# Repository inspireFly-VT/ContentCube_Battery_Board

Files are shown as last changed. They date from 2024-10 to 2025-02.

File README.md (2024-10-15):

View this project on [CADLAB.io](https://cadlab.io/project/28565). 

# battery_board
The battery and power management board for the PROVES Kit.
# Flight Heritage
| Version | Flights | Status |
| --- | --- | --- |
| V0 | Unflown | Not Supported |
| V1 | Unflown | Not Supported |
| V2 | Pleiades - Yearling, Pleaides - Squared | Supported |
| V3 | Planned Pleiades - Orpheus | In Development |
# Features
## battery_board_v2
The battery board flown on the Pleiades-Yearling and Pleiades-Squared missions. The board serves as an interface with the rest of the satellite. A 12 position picolock is utilized to interface between the Flight Controller and the Battery Board. The board interfaces with 5 solar faces of the satellite using 5 position picolocks. The other 2 position picolocks are used for interfacing with the inhibit scheme, battery heater, burn wire, and direct charging port. The hardware utilized on the module is the following:
- **LT3652 MPPT Solar Charger** is utilized to charge the batteries up from the solar faces. The Solar Charging circuitry should only allow higher potentials to be fed to the battery, and allow no reverse current into the charging circuitry.
- **PCA9685 LED Driver** is utilized to toggle the power to each of the solar faces. In the event that a sensor or other component fails on a face, it makes it possible to isolate the problem and power down the face.
- **TCA9548 I2C Multiplexer** is implemented to allow the use of a single I2C bus from the flight computer. This I2C bus can then get multiplexed to the solar faces. This allows the sensors on all of the faces to be the exact same, maintain the same addresses, and still be individually addressable. Two of the multiplexed lines are unused, 5 are used for each solar face, and 1 is used to breakout a stemma QT connection for additional sensors or I2C devices.
- **TPS54226PWP Switching Voltage Regulator** is utilized to maximize the efficiency of the system, and generate less heat central to the system. A 3.3V bus is created from the battery voltage and circuitry inspired by the PyCubed has been implemented to allow the satellite to reset the 3.3V bus. This functionality is known as the "One Shot" Regulator Reset that with a logic "High" applied, the 3.3V bus will shutdown and restart momentarily.
- **TPS7A4501 LDO Voltage Regulator** is implemented to supply 5V to the radio on the flight controller. This bus voltage can be toggled by an input taken from the flight controller.
- **(2) INA219 Power Monitors** are implemented to measure the power supplied from the solar cells, and the power dropped across the system. This data is fed back via the I2C bus to the flight controller
- **PTC2075 Temperature Sensor** is utilized to obtain ambient temperature readings from inside the satellite.
- **R5460N208AA** is utilized to disconnect the negative side of the batteries from the system in overcharge and overdischarge events.
- **APAN3109 Relay** is implemented to allow current to flow to the battery heater and burn wire MOSFETS.

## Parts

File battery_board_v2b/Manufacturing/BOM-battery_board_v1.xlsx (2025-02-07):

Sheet: battery_board_v2b
Id | Designator | Footprint | Quantity | Designation | JLC PN | Digikey PN | Inventory
3 | C1,C2 | C_0603_1608Metric | 2 | 22uF | C59461
31 | C10 | C_0603_1608Metric | 1 | 3.3nF | C1613
4 | C16,C15,C18,C12,C13 | C_0603_1608Metric | 5 | 10uF | C19702
8 | C17,C11 | C_0603_1608Metric | 2 | 1uF | C15849
60 | C22,C27 | C_0402_1005Metric_Pad0.74x0.62mm_HandSolder | 2 | 0.1uF | C60474
64 | C23,C21 | C_0402_1005Metric_Pad0.74x0.62mm_HandSolder | 2 | 0.01uF | C272878
48 | C24 | C_0402_1005Metric_Pad0.74x0.62mm_HandSolder | 1 | 1uF | C77006
35 | C26,C25 | C_0402_1005Metric_Pad0.74x0.62mm_HandSolder | 2 | 10uF | C15525
33 | C3,C4 | C_1210_3225Metric | 2 | 100uF | C23742
25 | C5,C6,C8,C9,C20,C7,C14 | C_0603_1608Metric | 7 | 0.1uF | C14663
71 | D3,D1 | DIOM5226X262N | 2 | D_Schottky | C2892544
6 | D5,D2,D4 | PWRDI-123 | 3 | DFLS130L | C110493
12 | FB1,FB3,FB2 | R_0603_1608Metric | 3 | FerriteBead |  | 490-5258-1-ND | 15 | “+3”
73 | IC1 | SOP65P640X110-28N | 1 | PCA9685PW,118 | C2678753
65 | IC2 | SOP65P490X110-13N | 1 | LT3652IMSE#PBF |  | 505-LT3652IMSE#PBF-ND
70 | IC3 | TSSOP-8_3x3mm_P0.65mm | 1 | PCT2075DP,118 | C192518
56 | J1 | MOLEX_5040500591 | 1 | Face0 |  | WM24877CT-ND
13 | J11,J13,J14,J15,J16,J17 | MOLEX_504050-0291 | 1 | CHARGE |  | WM25693CT-ND | 50
41 | J18 | PinSocket_1x02_P2.54mm_Vertical | 1 | Bypass
18 | J19 | MOLEX_504050-0291 | 1 | Heater |  | WM25693CT-ND
62 | J2,J3,J4 | MOLEX_5040500591 | 1 | Face1 |  | WM24877CT-ND | 25
5 | J6 | Molex_Pico-Lock_504050-1291_1x12-1MP_P1.50mm_Horizontal | 1 | FC_FACE |  | WM16219CT-ND | 5
26 | J7 | MOLEX_504050-0291 | 1 | 5V Breakout |  | WM25693CT-ND
54 | J8 | MOLEX_504050-0291 | 1 | ISS |  | WM25693CT-ND
57 | J9 | MOLEX_504050-0291 | 1 | TC |  | WM25693CT-ND
67 | K1 | RELAY_APAN3105 | 1 | APAN3105 |  | 255-5324-5-ND | 5
58 | L1 | L_1812_4532Metric | 1 | 3.3uH |  | 732-3063-1-ND | 5
59 | L2 | L_1812_4532Metric | 1 | 10uH |  | 732-3067-1-ND | 5
9 | Q2,Q1 | SOIC-8_3.9x4.9mm_P1.27mm | 2 | IRF7458 | C10879
11 | Q3,Q4 | SOT-363_SC-70-6 | 2 | MBT2222ADW1T1 | C157366
30 | Q6,Q9 | NDS8434 | 2 | SQ4401CEY-T1_GE3 |  | 742-SQ4401CEY-T1_GE3CT-ND | 4
10 | Q7 | SOT-523 | 1 | MMBT2222AT |  | MMBT2222ALT1GOSCT-ND | 5
49 | Q8,Q5 | SOT-23 | 2 | IRLML2803 | C2590
52 | R1 | R_2512_6332Metric | 1 | 0.01 |  | P19181CT-ND | 5
50 | R10 | R_0603_1608Metric | 1 | 20K | C408766
2 | R14,R40,R39,R50 | R_0603_1608Metric | 4 | 10k | C25804
20 | R2 | R_0603_1608Metric | 1 | 1K | C21190
53 | R22,R37 | R_2512_6332Metric | 2 | 0.002 |  | P17090CT-ND | 10
16 | R31 | R_0603_1608Metric | 1 | 3.3K | C22978
36 | R32 | R_0603_1608Metric | 1 | 200k | C25811
28 | R33 | R_0603_1608Metric | 1 | 85k |  | 2019-RN73R1JTTD8562F100CT-ND | 5
19 | R34,R44 | R_0603_1608Metric | 2 | 634k | C321970
74 | R35 | R_0603_1608Metric | 1 | 412k | C403212
63 | R36 | R_2512_6332Metric | 1 | 0.1 |  | YAG2159CT-ND | 10
46 | R4,R3 | R_0603_1608Metric | 2 | 330 | C23138
7 | R41,R16 | R_0603_1608Metric | 2 | 4.7k | C23162
66 | R42,R17,R9,R8,R11,R12,R13 | R_0603_1608Metric | 7 | 100k | C81751
1 | R43,R28,R25,R29,R19,R21,R30,R26,R15,R20,R23,R18,R27,R38,R24 | R_0603_1608Metric | 15 | 10K | C95204
24 | R46 | R_0402_1005Metric_Pad0.72x0.64mm_HandSolder | 1 | 1-MOhm | C93949
14 | R47,R48 | R_0402_1005Metric_Pad0.72x0.64mm_HandSolder | 2 | 100-Ohm | C106232
47 | R49 | R_0402_1005Metric_Pad0.72x0.64mm_HandSolder | 1 | 1k | C136974
45 | R6,R5 | R_0603_1608Metric | 2 | 73.2K | C861548
39 | R7 | R_0603_1608Metric | 1 | 22.1K | C137768
44 | U1 | R5460N233AF-SOT95P280X130-6N | 1 | R5460N208AA | C259714
29 | U10 | SOT-23 | 1 | TLVH431 DBZ SOT-23 |  | 296-36778-1-ND | 5
69 | U11 | TSSOP-10_3x3mm_P0.5mm | 1 | ADS1015IDGS |  | 296-25227-1-ND | 5
40 | U2 | PWP14_2P31X2P46-L | 1 | TPS54226PWPRPWP14_2P31X2P46-L |  | 296-25332-1-ND | 5
42 | U4 | SOP65P640X120-24N | 1 | TCA9548APWR | C130026
38 | IC4 | TPSM84209RKHT | 1 | TPSM84209RKHT | C2836944
55 | U6,U3 | SOIC-8_3.9x4.9mm_P1.27mm | 2 | INA219AxD | C138706
75 | U8,U7 | 1049 | 2 | 1049 |  | 36-1049-ND | 10
22 | U9 | MSOP-8_3x3mm_P0.65mm | 1 | AD8495 |  | AD8495ARMZ-R7CT-ND | 5
 | C19 | C_0603_1608Metric | 1 | 330pF | C1664
 | C28 | C_0603_1608Metric | 1 | 47uF | C140782
 | R45 | R_0603_1608Metric | 1 | 1.37k | C137777
 | Tool Hand Extractor |  |  |  |  |  | 1
 | Connection Socket 30 – 32AWG |  |  |  |  |  | 250
 | CONN RCPT HSG 2POS 1.50MM |  |  |  |  |  | 50
 | CONN RCPT HSG 4POS 1.50MM |  |  |  |  |  | 10
 | CONN RCPT HSG 5POS 1.50MM |  |  |  |  |  | 25
 | CONN RCPT HSG 6POS 1.50MM |  |  |  |  |  | 10
 | CONN RCPT HSG 12POS 1.50MM |  |  |  |  |  | 10

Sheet: BOM-battery_board_v1
Designation | Designator | Footprint | Supplier and ref
73.2K | R6,R5 | R_0603_1608Metric | C101180
100-Ohm | R47,R48 | R_0402_1005Metric_Pad0.72x0.64mm_HandSolder | C106232
IRF7458 | Q2,Q1 | SOIC-8_3.9x4.9mm_P1.27mm | C10879
22uF | C1,C2 | C_0603_1608Metric | C109448
DFLS130L | D5,D2,D4 | PWRDI-123 | C110493
TCA9548APWR | U4 | SOP65P640X120-24N | C130026
ADS1015IDGS | U11 | TSSOP-10_3x3mm_P0.5mm | C1355858
1k | R49 | R_0402_1005Metric_Pad0.72x0.64mm_HandSolder | C136974
INA219AxD | U6,U3 | SOIC-8_3.9x4.9mm_P1.27mm | C138706
22.1K | R7 | R_0603_1608Metric | C137768
0.1uF | C5,C6,C8,C9,C20,C7,C14 | C_0603_1608Metric | C14663
MBT2222ADW1T1 | Q3,Q4 | SOT-363_SC-70-6 | C157366
1uF | C17,C11 | C_0603_1608Metric | C15849
3.3nF | C10 | C_0603_1608Metric | C1613
PCT2075DP,118 | IC3 | TSSOP-8_3x3mm_P0.65mm | C192518
10uF | C16,C15,C18,C12 | C_0603_1608Metric | C19702
1K | R2 | R_0603_1608Metric | C21190
3.3K | R31 | R_0603_1608Metric | C22978
330 | R4,R3 | R_0603_1608Metric | C23138
4.7k | R41,R16 | R_0603_1608Metric | C23162
200uF | C19,C13 | C_1210_3225Metric | C23742
100uF | C3,C4 | C_1210_3225Metric | C23742
10k | R14,R40,R39 | R_0603_1608Metric | C25804
200k | R32 | R_0603_1608Metric | C25811
IRLML2803 | Q8,Q5 | SOT-23 | C2590
R5460N208AA | U1 | R5460N233AF-SOT95P280X130-6N | C259714
PCA9685PW,118 | IC1 | SOP65P640X110-28N | C2678753
0.01uF | C23,C21 | C_0402_1005Metric_Pad0.74x0.62mm_HandSolder | C272878
D_Schottky | D3,D1 | DIOM5226X262N | C2892544
412k | R35 | R_0603_1608Metric | C403212
634k | R34,R44 | R_0603_1608Metric | C321970
20K | R10 | R_0603_1608Metric | C408766
0.1uF | C22,C27 | C_0402_1005Metric_Pad0.74x0.62mm_HandSolder | C60474
1uF | C24 | C_0402_1005Metric_Pad0.74x0.62mm_HandSolder | C77006
100k | R42,R17,R9,R8,R11,R12,R13 | R_0603_1608Metric | C81751
TPS7A4501DCQT | U5 | TPS7A4501DCQT | C840094
1-MOhm | R46 | R_0402_1005Metric_Pad0.72x0.64mm_HandSolder | C93949
10K | R43,R28,R25,R29,R19,R21,R30,R26,R15,R20,R23,R18,R27,R38,R24 | R_0603_1608Metric | C95204
10uF | C26,C25 | C_0402_1005Metric_Pad0.74x0.62mm_HandSolder | C962136

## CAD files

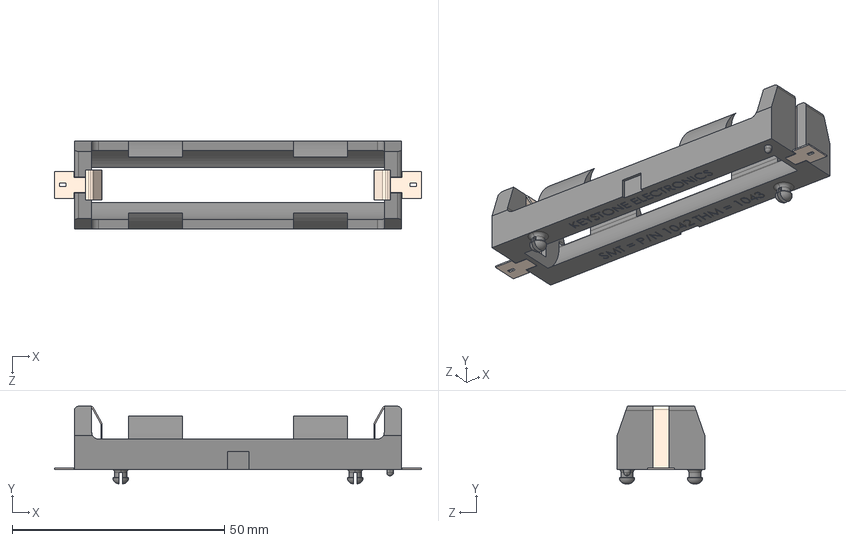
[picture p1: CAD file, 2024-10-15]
battery_board_v2b/Footprints/1042 (NOT OPEN SOURCE)/1042.stp
86.4 x 18.3 x 20.6 mm

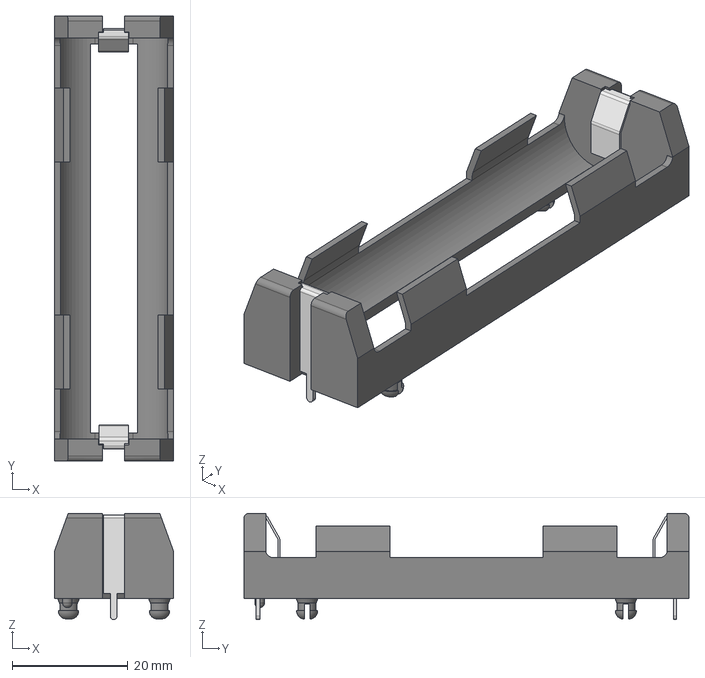
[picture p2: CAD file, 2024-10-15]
battery_board_v2b/Footprints/1043 (NOT OPEN SOURCE)/1043.stp
20.6 x 77.0 x 18.4 mm

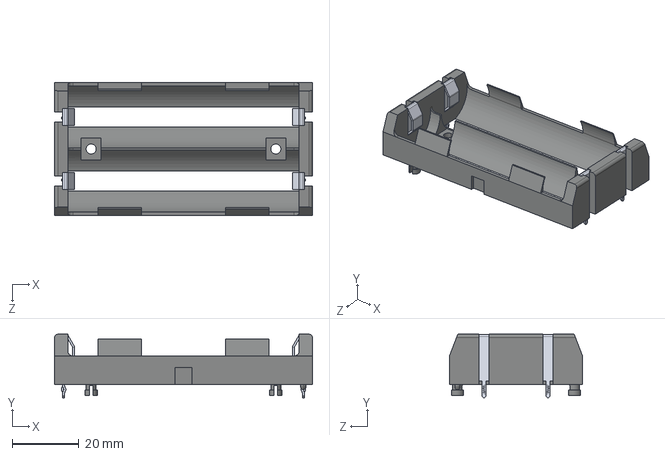
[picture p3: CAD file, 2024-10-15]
battery_board_v2b/Footprints/1049 (NOT OPEN SOURCE)/3D/1049.stp
77.1 x 19.0 x 39.8 mm

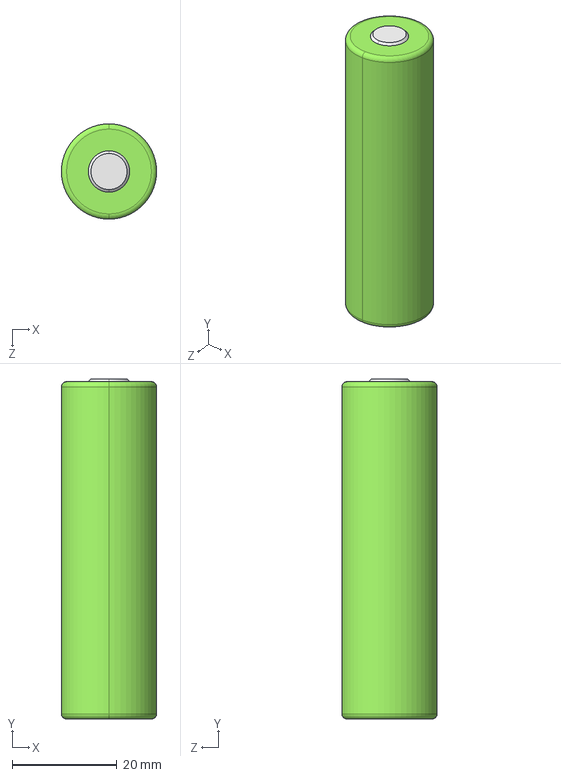
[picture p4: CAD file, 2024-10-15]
battery_board_v2b/Footprints/18650/Panasonic_NCR18650B_Battery-Gabriella.STEP
18.2 x 64.9 x 18.2 mm

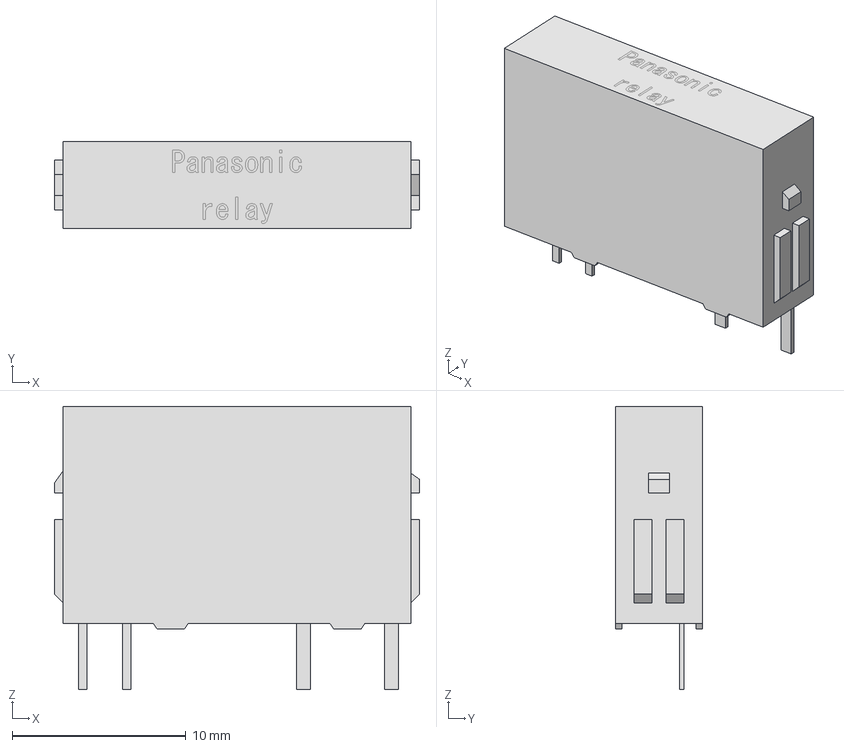
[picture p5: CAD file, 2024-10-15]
battery_board_v2b/Footprints/APAN/apan31・・.step
21.0 x 5.00 x 16.3 mm

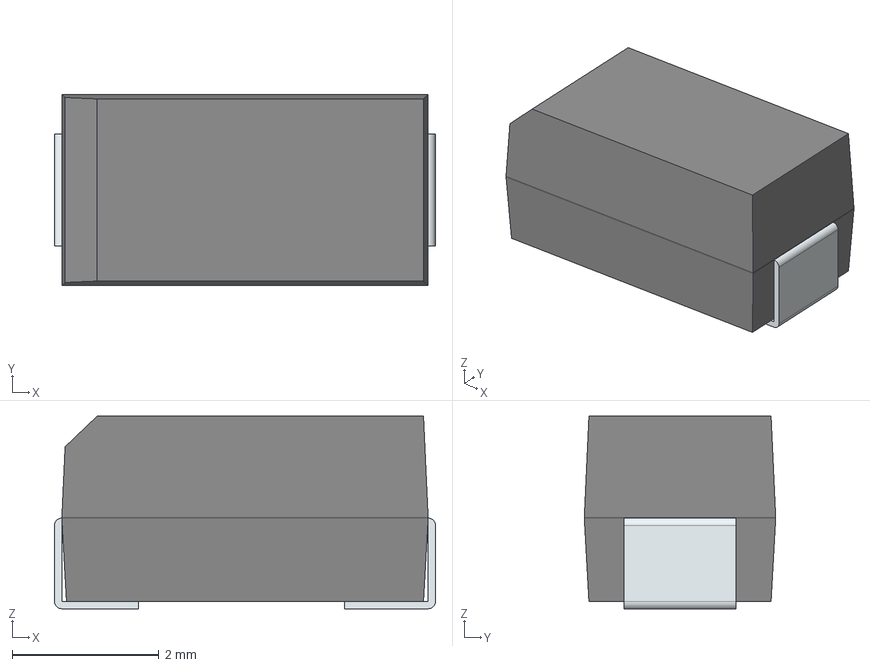
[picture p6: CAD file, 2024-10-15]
battery_board_v2b/Footprints/LIB_CMSH3-40MA_TR13_PBFREE/CMSH3-40MA_TR13_PBFREE/3D/CMSH3-40MA_TR13_PBFREE.stp
5.18 x 2.60 x 2.62 mm
FilletPin1
FilletPin2

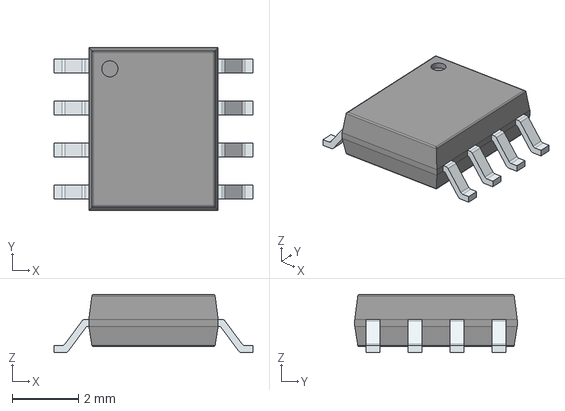
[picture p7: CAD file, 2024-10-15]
battery_board_v2b/Footprints/LIB_IRF7105TRPBF/IRF7105TRPBF/3D/IRF7105TRPBF.stp
6.00 x 4.90 x 1.75 mm
PinsArrayLR

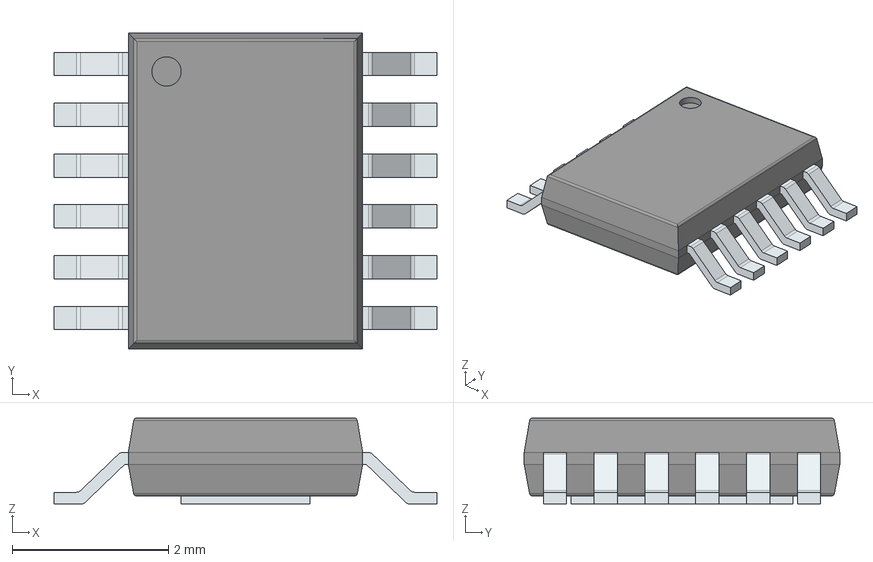
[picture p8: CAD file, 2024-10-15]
battery_board_v2b/Footprints/LIB_LT3652IMSE#PBF/LT3652IMSE#PBF/3D/LT3652IMSE#PBF.stp
4.90 x 4.04 x 1.10 mm
PinsArrayLR
ThermalPad

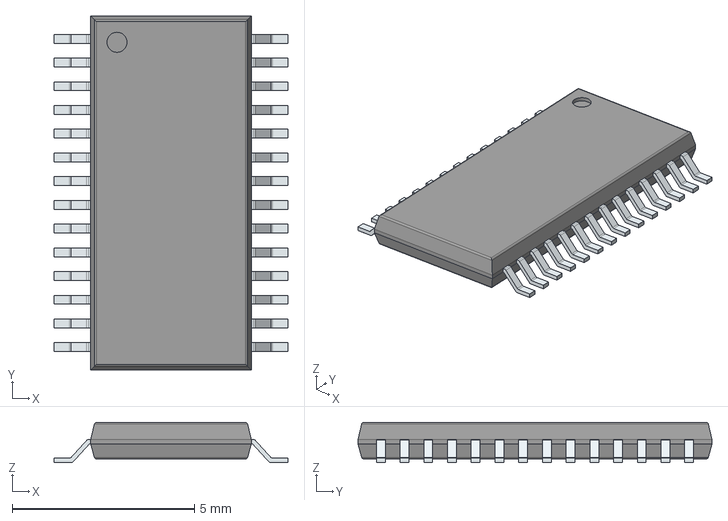
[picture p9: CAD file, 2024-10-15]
battery_board_v2b/Footprints/LIB_PCA9685PW,118/PCA9685PW,118/3D/PCA9685PW,118.stp
6.40 x 9.70 x 1.10 mm
PinsArrayLR

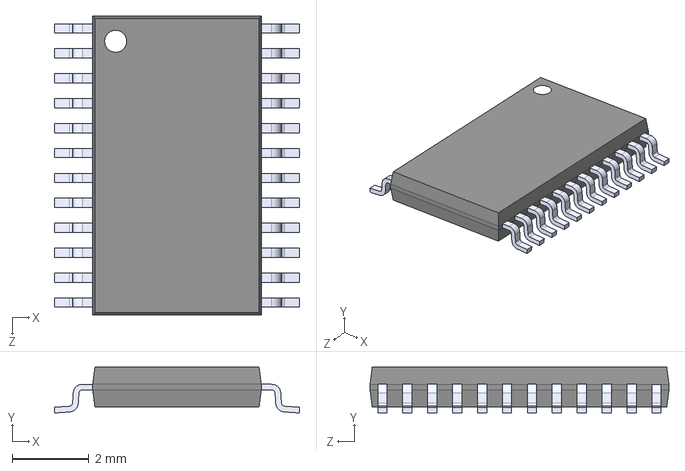
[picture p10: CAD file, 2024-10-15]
battery_board_v2b/Footprints/TCA9548APWR/TCA9548APWR.step
6.40 x 1.20 x 7.80 mm

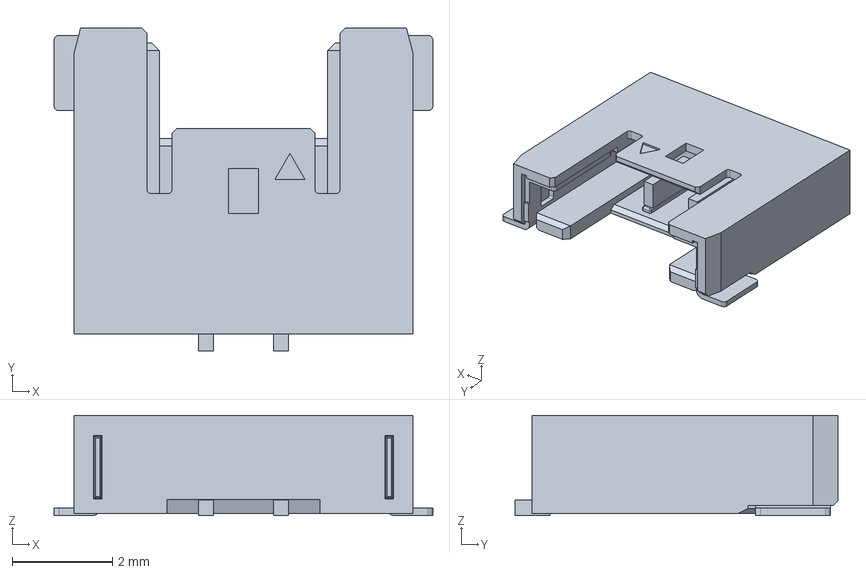
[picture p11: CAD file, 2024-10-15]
battery_board_v2b/Footprints/504050-0291/504050-0291.step
7.55 x 6.44 x 2.00 mm

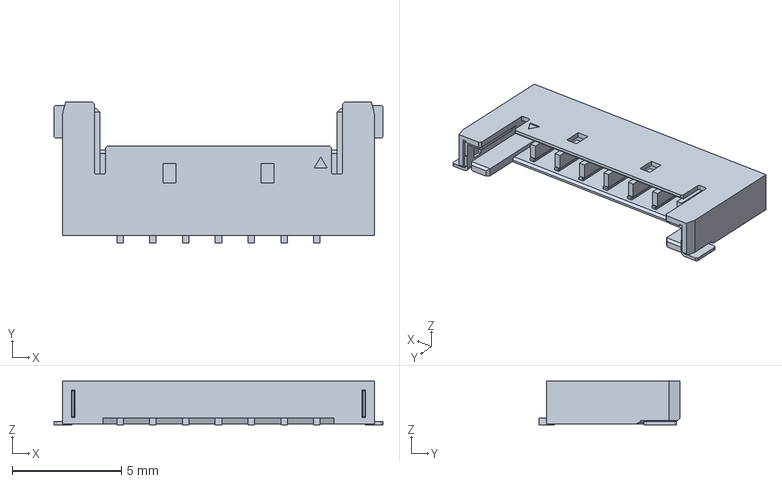
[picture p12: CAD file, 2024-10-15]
battery_board_v2b/Footprints/5040500791/5040500791.step
15.1 x 6.44 x 2.00 mm

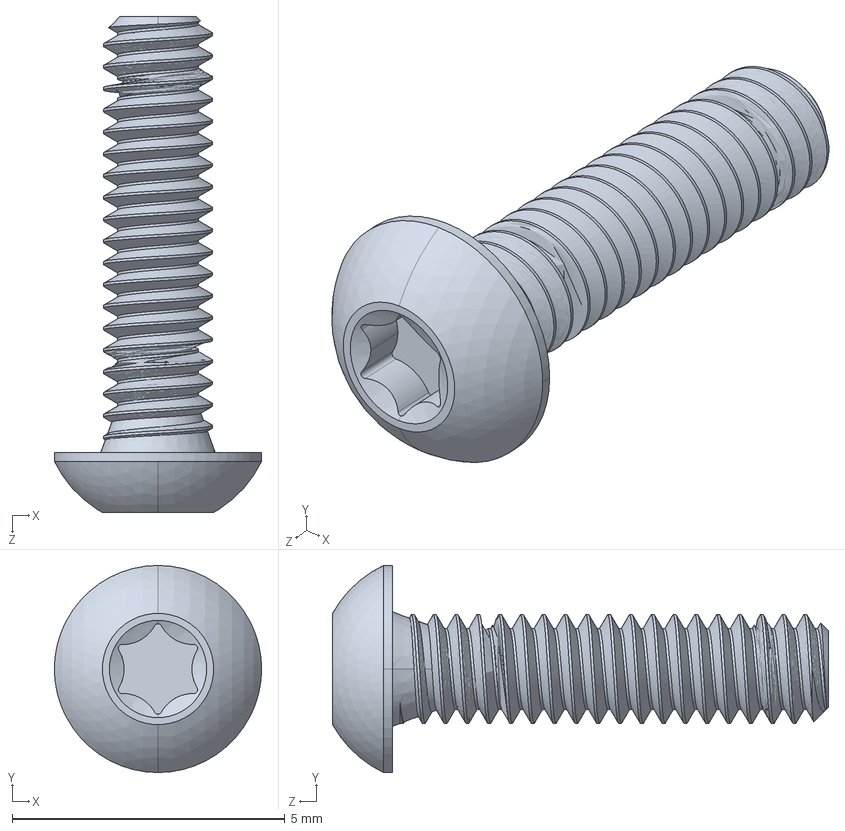
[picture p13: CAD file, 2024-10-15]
battery_board_v2b/Footprints/McMaster/90910A923_Button Head Torx Screws.STEP
3.80 x 3.80 x 9.10 mm

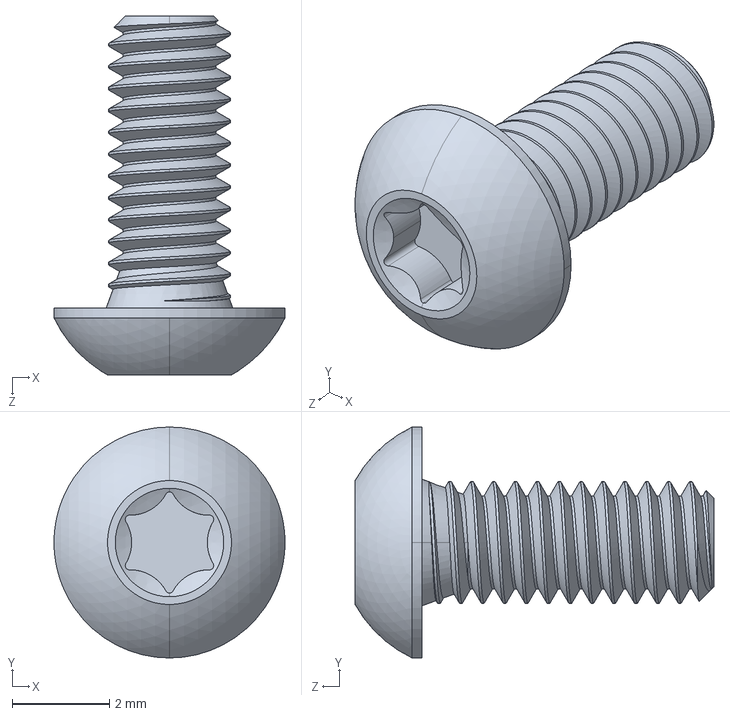
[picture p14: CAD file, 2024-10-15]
battery_board_v2b/Footprints/McMaster/90910A941_Button Head Torx Screws.STEP
4.75 x 4.75 x 7.38 mm

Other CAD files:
battery_board_v2b/Footprints/APAN3105/APAN3105.step
battery_board_v2b/Footprints/Pico Lock (NOT OPEN SOURCE)/504050-0291.stp
battery_board_v2b/Footprints/Pico Lock (NOT OPEN SOURCE)/504050-0591.stp
battery_board_v2b/Footprints/McMaster/90362A147_18-8 Stainless Steel Pan Head Torx Screws.STEP
battery_board_v2b/Footprints/LIB_CMSH3-40MA_TR13_PBFREE/CMSH3-40MA_TR13_PBFREE/Allegro/diom5226x262n.psm
battery_board_v2b/Footprints/LIB_CMSH3-40MA_TR13_PBFREE/CMSH3-40MA_TR13_PBFREE/DEHDL/cmsh3_40ma_tr13_pbfree/chips/chips.prt
battery_board_v2b/Footprints/LIB_IRF7105TRPBF/IRF7105TRPBF/Allegro/soic127p600x175-8n.psm
battery_board_v2b/Footprints/LIB_IRF7105TRPBF/IRF7105TRPBF/DEHDL/irf7105trpbf/chips/chips.prt
battery_board_v2b/Footprints/LIB_LT3652IMSE#PBF/LT3652IMSE#PBF/Allegro/sop65p490x110-13n.psm
battery_board_v2b/Footprints/LIB_LT3652IMSE#PBF/LT3652IMSE#PBF/DEHDL/lt3652imse#pbf/chips/chips.prt
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

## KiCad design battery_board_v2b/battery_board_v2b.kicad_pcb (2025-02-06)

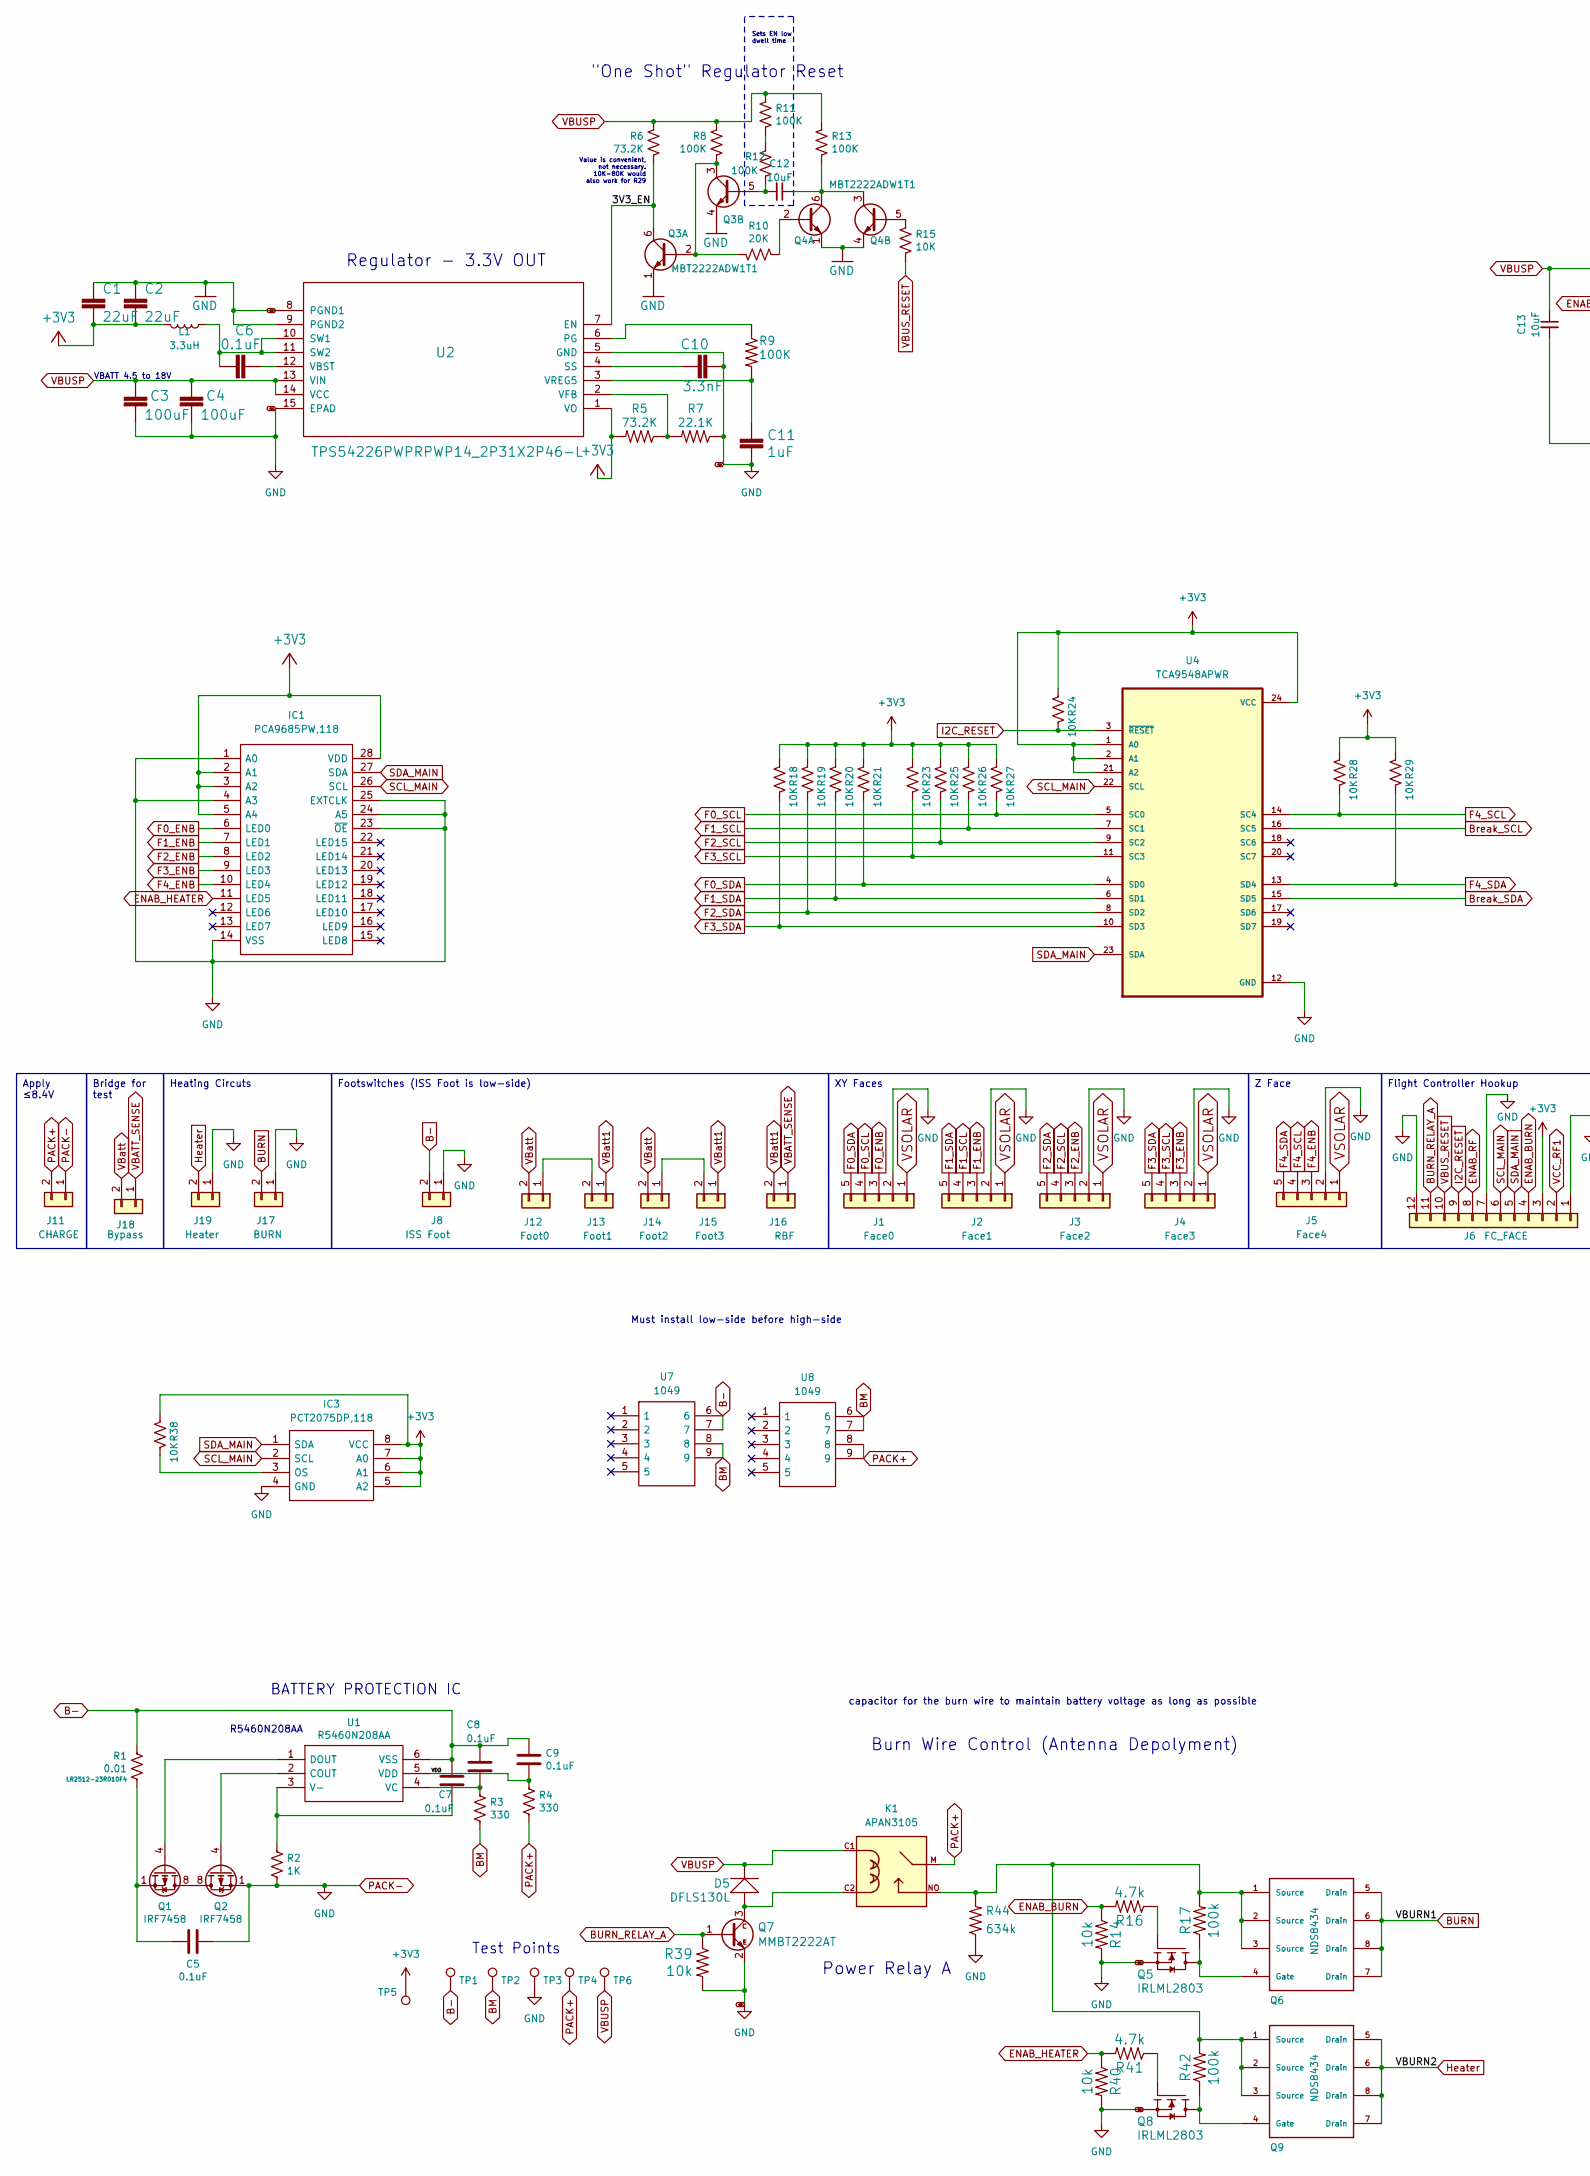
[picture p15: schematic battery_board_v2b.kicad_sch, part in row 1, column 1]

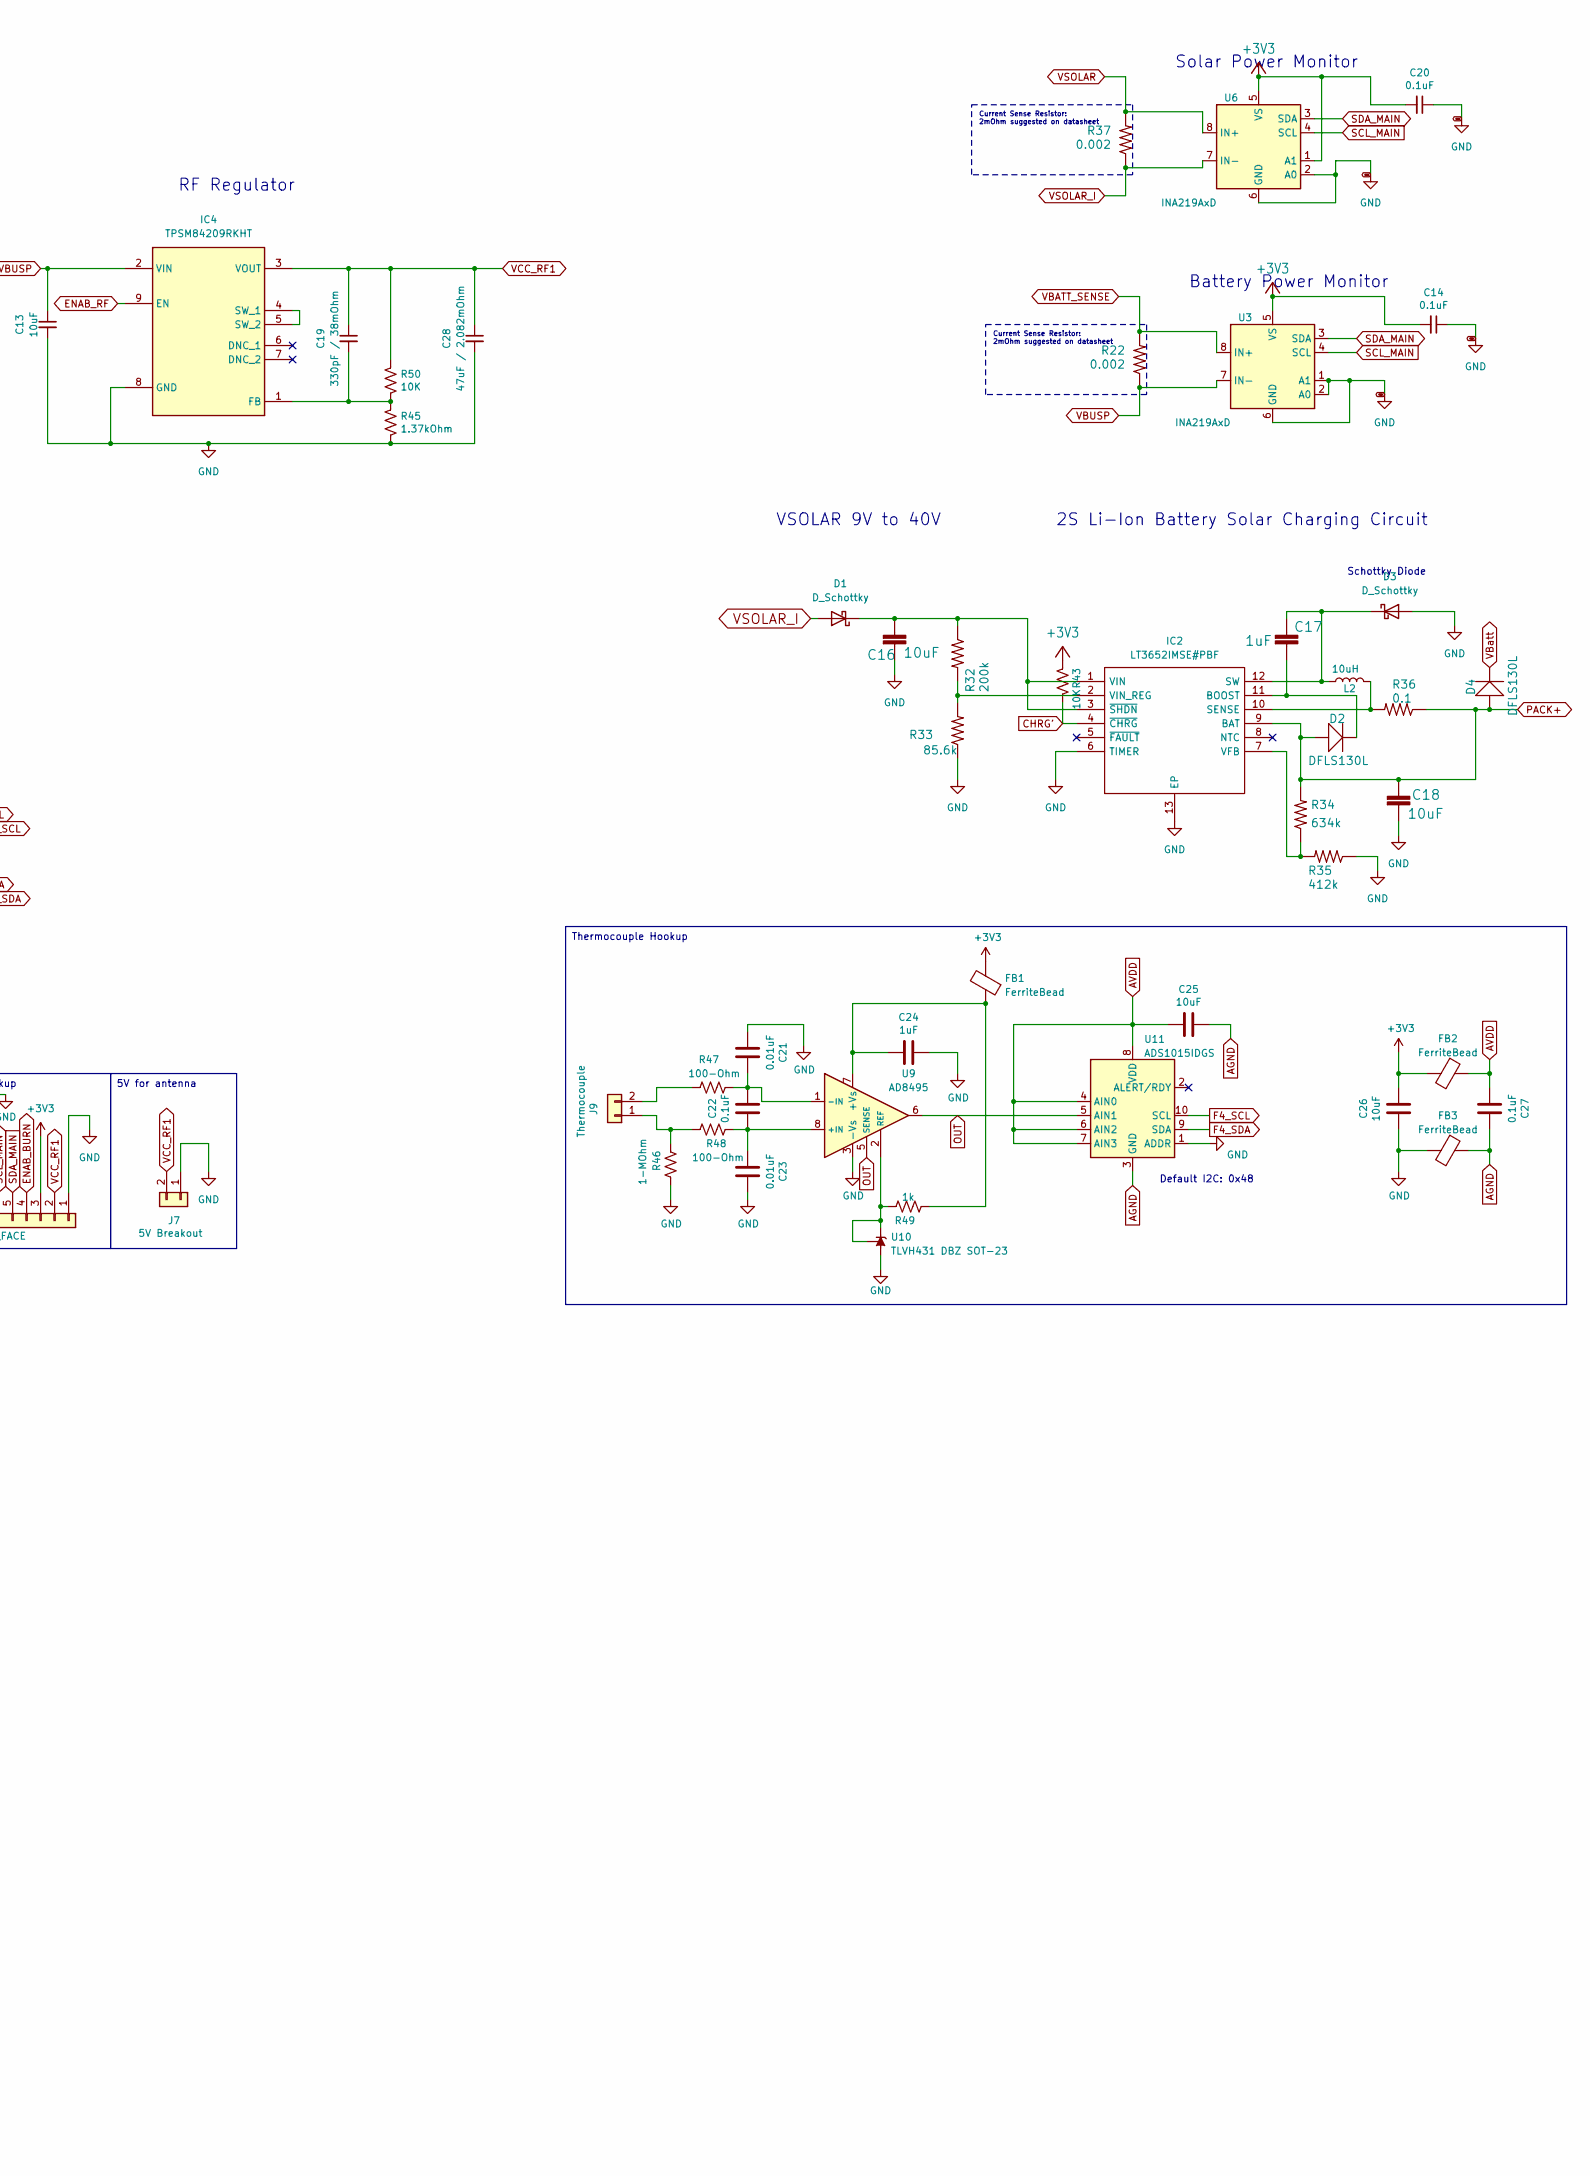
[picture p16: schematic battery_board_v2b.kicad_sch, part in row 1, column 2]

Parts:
C1, C2: 22uF; C_0603_1608Metric
C3, C4: 100uF; C_1210_3225Metric
C5, C6, C7, C8, C9, C14, C20: 0.1uF; C_0603_1608Metric
C10: 3.3nF; C_0603_1608Metric
C11, C17: 1uF; C_0603_1608Metric
C12, C13, C16, C18: 10uF; C_0603_1608Metric
C19: 330pF / 38mOhm; C_0603_1608Metric
C21, C23: 0.01uF; C_0402_1005Metric_Pad0.74x0.62mm_HandSolder
C22, C27: 0.1uF; C_0402_1005Metric_Pad0.74x0.62mm_HandSolder
C24: 1uF; C_0402_1005Metric_Pad0.74x0.62mm_HandSolder
C25, C26: 10uF; C_0402_1005Metric_Pad0.74x0.62mm_HandSolder
C28: 47uF / 2.082mOhm; C_0603_1608Metric
D1, D3: D_Schottky; DIOM5226X262N
D2, D4, D5: DFLS130L; PWRDI-123; Manufacturer_Part_Number DFLS130L-7
FB1, FB2, FB3: FerriteBead; R_0603_1608Metric
IC1: PCA9685PW,118; SOP65P640X110-28N; Mouser Part Number 771-PCA9685PW,118
IC2: LT3652IMSE#PBF; SOP65P490X110-13N; Mouser Part Number 584-LT3652IMSE#PBF
IC3: PCT2075DP,118; TSSOP-8_3x3mm_P0.65mm; Mouser Part Number 771-PCT2075DP118
IC4: TPSM84209RKHT; Mouser Part Number 595-TPSM84209RKHT
J1: Face0; MOLEX_5040500591
J2: Face1; MOLEX_5040500591
J3: Face2; MOLEX_5040500591
J4: Face3; MOLEX_5040500591
J5: Face4; MOLEX_5040500591
J6: FC_FACE; Molex_Pico-Lock_504050-1291_1x12-1MP_P1.50mm_Horizontal
J7: 5V Breakout; MOLEX_504050-0291
J8: ISS Foot; MOLEX_504050-0291
J9: Thermocouple; MOLEX_504050-0291
J11: CHARGE; MOLEX_504050-0291
J12: Foot0; MOLEX_504050-0291
J13: Foot1; MOLEX_504050-0291
J14: Foot2; MOLEX_504050-0291
J15: Foot3; MOLEX_504050-0291
J16: RBF; MOLEX_504050-0291
J17: BURN; MOLEX_504050-0291
J18: Bypass; PinSocket_1x02_P2.54mm_Vertical
J19: Heater; MOLEX_504050-0291
K1: APAN3105; RELAY_APAN3105
L1: 3.3uH; L_1812_4532Metric; Manufacturer_Part_Number HPC5040NF-3R3MTH
L2: 10uH; L_1812_4532Metric; Manufacturer_Part_Number SNR5040K-330M
Q1, Q2: IRF7458; SOIC-8_3.9x4.9mm_P1.27mm
Q3, Q4: MBT2222ADW1T1; SOT-363_SC-70-6; Manufacturer_Part_Number MBT2222ADW1T1G
Q5, Q8: IRLML2803; SOT-23; Manufacturer_Part_Number MMBT2222AT
Q6, Q9: NDS8434; Manufacturer_Part_Number NDS8434
Q7: MMBT2222AT; SOT-523; Manufacturer_Part_Number MMBT2222ALT1G
R1: 0.01; R_2512_6332Metric
R2: 1K; R_0603_1608Metric
R3, R4: 330; R_0603_1608Metric
R5, R6: 73.2K; R_0603_1608Metric
R7: 22.1K; R_0603_1608Metric
R8, R9, R11, R12, R13: 100K; R_0603_1608Metric
R10: 20K; R_0603_1608Metric
R14, R39, R40: 10k; R_0603_1608Metric
R15, R18, R19, R20, R21, R23, R24, R25, R26, R27, R28, R29, R38, R43, R50: 10K; R_0603_1608Metric
R16, R41: 4.7k; R_0603_1608Metric
R17, R42: 100k; R_0603_1608Metric
R22, R37: 0.002; R_2512_6332Metric
R32: 200k; R_0603_1608Metric
R33: 85.6k; R_0603_1608Metric
R34, R44: 634k; R_0603_1608Metric
R35: 412k; R_0603_1608Metric
R36: 0.1; R_2512_6332Metric
R45: 1.37kOhm; R_0603_1608Metric
R46: 1-MOhm; R_0402_1005Metric_Pad0.72x0.64mm_HandSolder
R47, R48: 100-Ohm; R_0402_1005Metric_Pad0.72x0.64mm_HandSolder
R49: 1k; R_0402_1005Metric_Pad0.72x0.64mm_HandSolder
TP1, TP2, TP3, TP4, TP5, TP6: TestPoint; TestPoint_Loop_D1.80mm_Drill1.0mm_Beaded
U1: R5460N208AA; R5460N233AF-SOT95P280X130-6N; Manufacturer_Part_Number R5460N233AF-TR-FE; Mouser Part Number 848-R5460N233AFTRFE
U2: TPS54226PWPRPWP14_2P31X2P46-L; PWP14_2P31X2P46-L; Manufacturer_Part_Number TPS54226PWPR
U3, U6: INA219AxD; SOIC-8_3.9x4.9mm_P1.27mm
U4: TCA9548APWR; SOP65P640X120-24N
U7, U8: 1049; Mouser Part Number 534-1049
U9: AD8495; MSOP-8_3x3mm_P0.65mm
U10: TLVH431 DBZ SOT-23; SOT-23
U11: ADS1015IDGS; TSSOP-10_3x3mm_P0.5mm

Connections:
/3V3_EN: Q3.6 (C1), R6.2, U2.7 (EN)
/VDD: C9.2, R4.2, U1.5 (VDD)
AGND: C25.2, C27.2, FB3.1, U11.3 (GND)
AVDD: C25.1, C27.1, FB2.1, U11.4 (AIN0), U11.6 (AIN2), U11.7 (AIN3), U11.8 (VDD)
BM: R3.1, TP2.1, U7.8, U7.9, U8.6, U8.7
BURN: J17.2, Q6.5 (Drain), Q6.6 (Drain), Q6.7 (Drain), Q6.8 (Drain)
BURN_RELAY_A: J6.11, Q7.1 (B), R39.1
Break_SCL: U4.16 (SC5)
Break_SDA: U4.15 (SD5)
CHRG': IC2.4 (~CHRG), R43.2
ENAB_BURN: J6.4, R14.1, R16.2
ENAB_HEATER: IC1.11 (LED5), R40.1, R41.2
ENAB_RF: IC4.9 (EN), J6.8
F0_ENB: IC1.6 (LED0), J1.3
F0_SCL: J1.4, R27.2, U4.5 (SC0)
F0_SDA: J1.5, R21.2, U4.4 (SD0)
F1_ENB: IC1.7 (LED1), J2.3
F1_SCL: J2.4, R26.2, U4.7 (SC1)
F1_SDA: J2.5, R20.2, U4.6 (SD1)
F2_ENB: IC1.8 (LED2), J3.3
F2_SCL: J3.4, R25.2, U4.9 (SC2)
F2_SDA: J3.5, R19.2, U4.8 (SD2)
F3_ENB: IC1.9 (LED3), J4.3
F3_SCL: J4.4, R23.2, U4.11 (SC3)
F3_SDA: J4.5, R18.2, U4.10 (SD3)
F4_ENB: IC1.10 (LED4), J5.3
F4_SCL: J5.4, R28.2, U4.14 (SC4), U11.10 (SCL)
F4_SDA: J5.5, R29.2, U4.13 (SD4), U11.9 (SDA)
Heater: J19.2, Q9.5 (Drain), Q9.6 (Drain), Q9.7 (Drain), Q9.8 (Drain)
I2C_RESET: J6.9, R24.2, U4.3 (~RESET)
unnamed: C5.1, Q1.1 (S), Q1.2 (S), Q1.3 (S), R1.2
unnamed: C16.1, D1.1 (K), IC2.1 (VIN), IC2.3 (~SHDN), R32.1
unnamed: C17.1, D3.1 (K), IC2.12 (SW), L2.1
unnamed: C17.2, D2.C, IC2.11 (BOOST)
unnamed: IC2.10 (SENSE), L2.2, R36.2
unnamed: IC2.7 (VFB), R34.1, R35.2
unnamed: IC2.2 (VIN_REG), R32.2, R33.2
unnamed: IC3.3 (OS), R38.2
unnamed: C19.2, IC4.1 (FB), R45.1, R50.2
unnamed: IC4.4 (SW_1), IC4.5 (SW_2)
unnamed: J9.1, R46.1, R48.2
unnamed: J9.2, R47.1
unnamed: J12.1, J13.2
unnamed: J14.1, J15.2
unnamed: K1.NO, Q6.1 (Source), Q6.2 (Source), Q6.3 (Source), Q9.1 (Source), Q9.2 (Source), Q9.3 (Source), R17.2, R42.2, R44.2
unnamed: Q1.5 (D), Q1.6 (D), Q1.7 (D), Q1.8 (D), Q2.5 (D), Q2.6 (D), Q2.7 (D), Q2.8 (D)
unnamed: Q1.4 (G), U1.1 (DOUT)
unnamed: Q2.4 (G), U1.2 (COUT)
unnamed: Q3.2 (B1), Q3.3 (C2), R8.2, R10.2
unnamed: C12.2, Q3.5 (B2), R12.2
unnamed: Q4.2 (B1), R10.1
unnamed: C12.1, Q4.3 (C2), Q4.6 (C1), R13.2
unnamed: Q4.5 (B2), R15.1
unnamed: Q5.3 (D), Q6.4 (Gate), R17.1
unnamed: Q5.1 (G), R16.1
unnamed: D5.A, K1.C2, Q7.3 (C)
unnamed: Q8.3 (D), Q9.4 (Gate), R42.1
unnamed: Q8.1 (G), R41.1
unnamed: R11.2, R12.1
unnamed: C7.2, R2.1, U1.3 (V-)
unnamed: C8.2, R3.2, U1.4 (VC)
unnamed: R9.1, U2.6 (PG)
unnamed: C10.1, U2.4 (SS)
unnamed: C6.1, L1.1, U2.10 (SW1), U2.11 (SW2)
unnamed: C6.2, U2.12 (VBST)
unnamed: R5.1, R7.2, U2.2 (VFB)
unnamed: C11.1, R9.2, U2.3 (VREG5)
unnamed: C22.1, C23.1, R48.1, U9.8 (+IN)
unnamed: C24.1, FB1.1, R49.2, U9.7 (+Vs)
unnamed: C21.2, C22.2, R47.2, U9.1 (-IN)
unnamed: R49.1, U9.2 (REF), U10.1 (K), U10.2 (REF)
OUT: U9.5 (SENSE), U9.6, U11.5 (AIN1)
PACK+: C18.1, D2.A, D4.A, IC2.9 (BAT), J11.2, K1.M, R4.1, R34.2, R36.1, TP4.1, U8.8, U8.9
SCL_MAIN: IC1.26 (SCL), IC3.2 (SCL), J6.6, U3.4 (SCL), U4.22 (SCL), U6.4 (SCL)
SDA_MAIN: IC1.27 (SDA), IC3.1 (SDA), J6.5, U3.3 (SDA), U4.23 (SDA), U6.3 (SDA)
VBATT_SENSE: J16.1, J18.1, R22.2, U3.8 (IN+)
VBUSP: C3.1, C4.1, C13.1, D5.C, IC4.2 (VIN), K1.C1, R6.1, R8.1, R11.1, R13.1, R22.1, TP6.1, U2.13 (VIN), U2.14 (VCC), U3.7 (IN-)
VBUS_RESET: J6.10, R15.2
VBatt: D4.C, J12.2, J14.2, J18.2
VBatt1: J13.1, J15.1, J16.2
VCC_RF1: C19.1, C28.1, IC4.3 (VOUT), J6.2, J7.2, R50.1
VSOLAR: J1.1, J2.1, J3.1, J4.1, J5.1, R37.2, U6.8 (IN+)
VSOLAR_I: D1.2 (A), R37.1, U6.7 (IN-)

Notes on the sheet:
Thermocouple Hookup
XY Faces
Footswitches (ISS Foot is low-side)
Z Face
Heating Circuts
Apply ≤8.4V
Bridge for test
Flight Controller Hookup
5V for antenna
Must install low-side before high-side
Test Points
Current Sense Resistor: 2mOhm suggested on datasheet
"One Shot" Regulator Reset
VSOLAR 9V to 40V
Regulator - 3.3V OUT
Battery Power Monitor
Solar Power Monitor
Sets EN low dwell time
Default I2C: 0x48
BATTERY PROTECTION IC
2S Li-Ion Battery Solar Charging Circuit
R5460N208AA
Burn Wire Control (Antenna Depolyment)
Power Relay A
capacitor for the burn wire to maintain battery voltage as long as possible
Value is convenient, not necessary. 10K-80K would also work for R29
RF Regulator
Schottky Diode
VBATT 4.5 to 18V

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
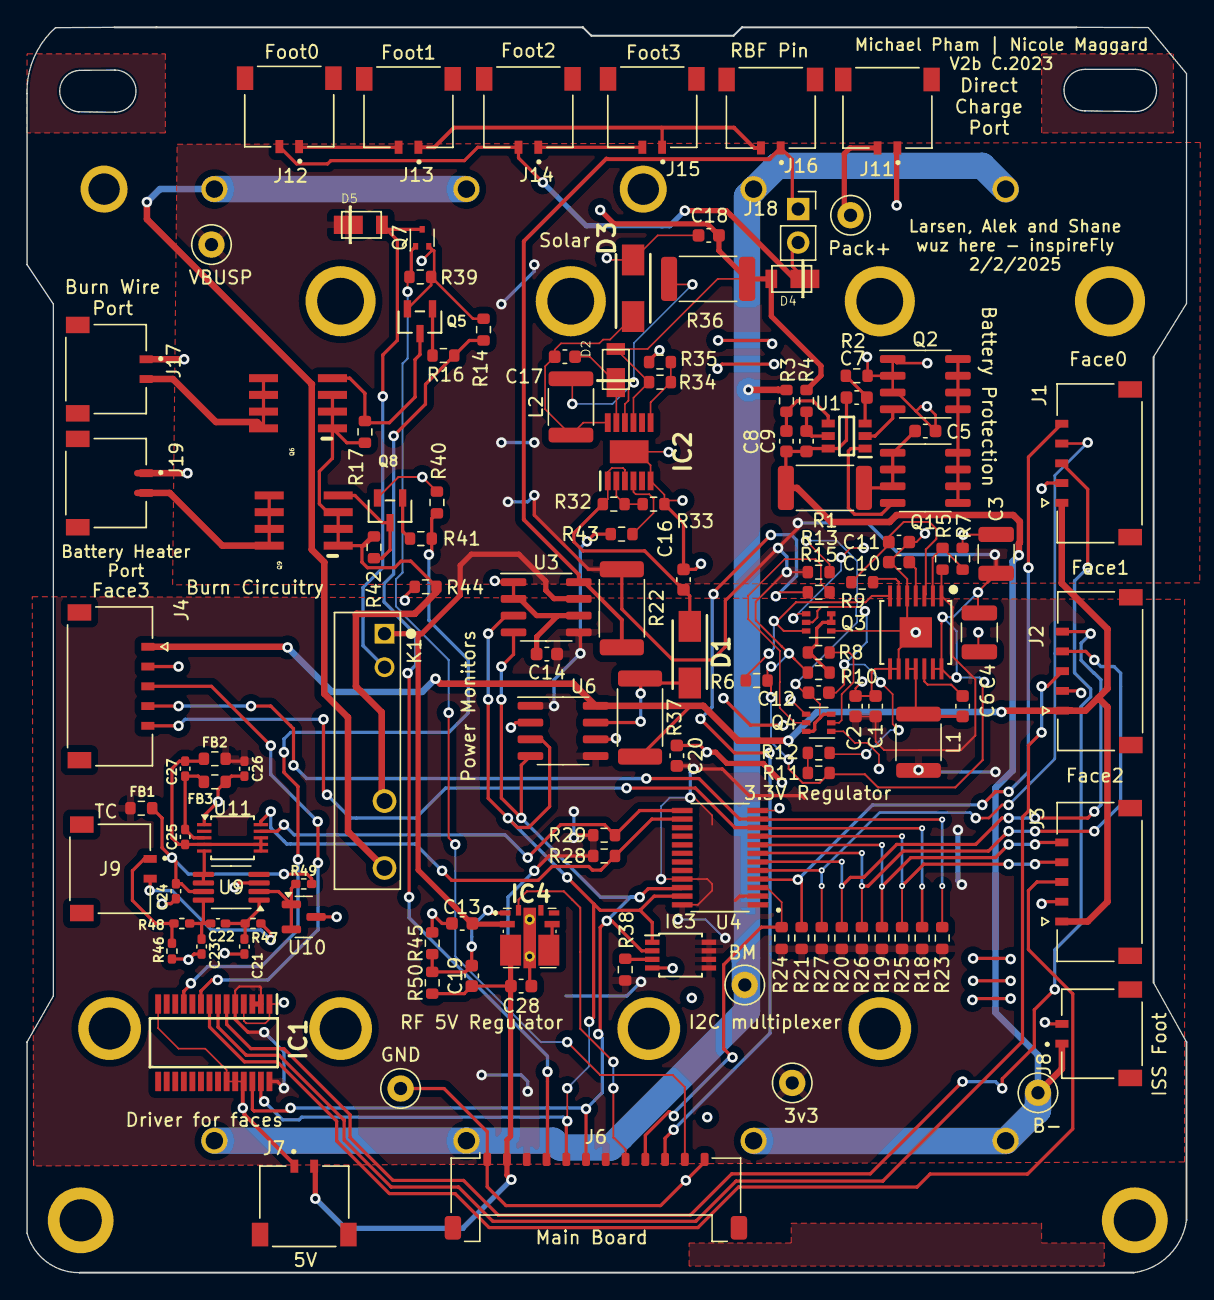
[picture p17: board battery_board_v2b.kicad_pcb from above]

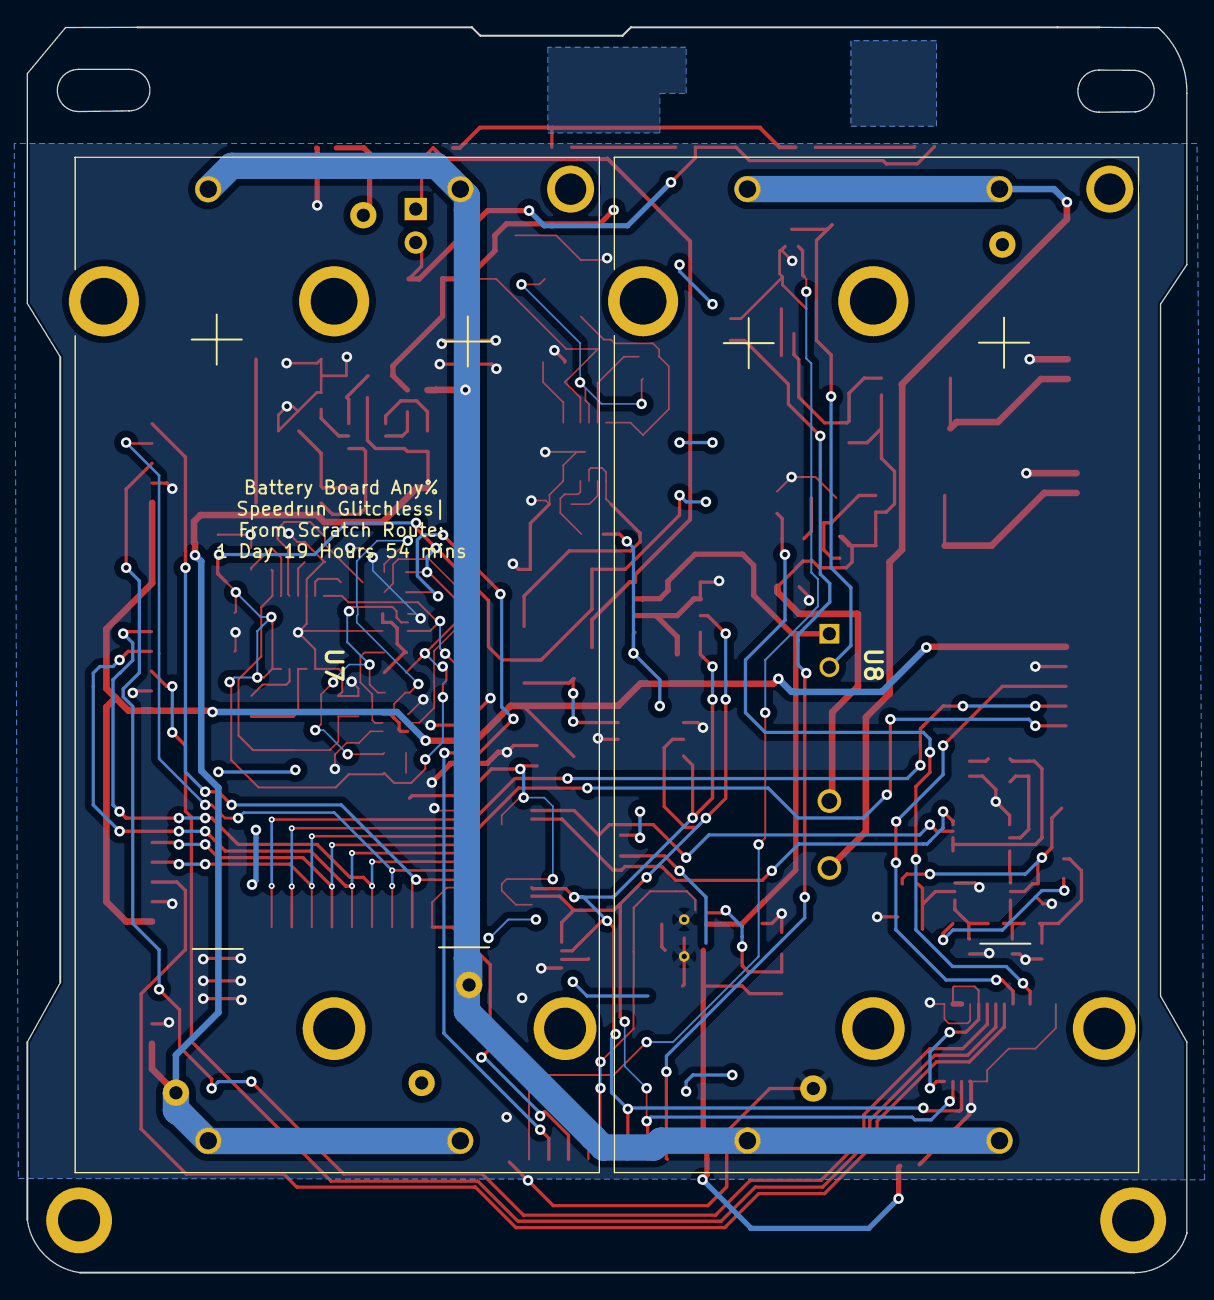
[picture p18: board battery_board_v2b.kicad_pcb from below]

Board: 4 copper layers, 88.0 x 94.5 mm, 132 parts (2 on the bottom side), 83 nets.

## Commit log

2024-10-15 Add Custom Battery Board Add Custom Battery Board with 5v rail and ISS foot switch.
    [battery_board_v1a1.kicad_pcb, battery_board_v1a1.kicad_sch, battery_board_v2a.kicad_pcb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]
2024-10-15 Add Custom Battery Board inspireFly Custom battery board that has 5v output and ISS footswitch
    [1042.stp, 1043.stp, 1049.stp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]
2024-10-23 Updated to add thermocouple driver onboard
    [battery_board_v2b.kicad_pcb, battery_board_v2b.kicad_sch]
2024-10-23 Placed the thermocoupler circuitry on the board and modified schematic FOr the schematic I removed the adresse jumper ase we know which I2C adresse we are using.
    [battery_board_v2b.kicad_pcb, battery_board_v2b.kicad_sch]
2024-11-10 Updated for JLC Manufacturing
    [battery_board_v2b-B_Cu.gbr, battery_board_v2b-B_Mask.gbr, battery_board_v2b-B_Paste.gbr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]
2024-11-10 Update .gitignore to add BOM files
2024-11-10 Added BOM Files
    [BOM-battery_board_v1.csv, battery_board_v2b.csv]
2024-11-10 Update BOM with part numbers and replace obsolete parts
    [BOM-battery_board_v1.csv, BOM-battery_board_v1.xlsx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]
2024-11-17 Updated BOM to reflect parts availability
    [BOM-battery_board_v1.xlsx, battery_board_v2b.kicad_pcb, battery_board_v2b.kicad_sch]
2024-11-26 Updated BOM
    [BOM-battery_board_v1.xlsx]
2024-11-26 Update BOM for final parts order
    [BOM-battery_board_v1.xlsx]
2025-02-03 Reliability Improvements
    [1042.stp, 1043.stp, 1049.stp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]
2025-02-03 Changed the 5V buck converter to a more efficient one
    [battery_board_v2b.kicad_pcb, battery_board_v2b.kicad_sch]
2025-02-03 Updated 5v reg and lowside switch
    [BOM-battery_board_v1.csv, BOM-battery_board_v1.xlsx, battery_board_v2b.kicad_pcb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]
2025-02-03 Updated files for manufacturing
    [BOM-JLC-battery_board_v1.csv, BOM-battery_board_v1.xlsx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]
2025-02-06 Changed pinout for the fc connector
    [battery_board_v2b.kicad_pcb]
2025-02-07 Added part count
    [BOM-battery_board_v1.xlsx]
